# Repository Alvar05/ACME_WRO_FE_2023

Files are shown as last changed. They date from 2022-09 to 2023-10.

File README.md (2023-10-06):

Engineering materials
====
## Introduction

This repository provides information about the building and programming process of our self-driving car for the Future Engineers 2023 competition. Since this is our third year participating in this competition we have updated our robot even more to be more controllable, compact and precise, remaking it almost entirely.

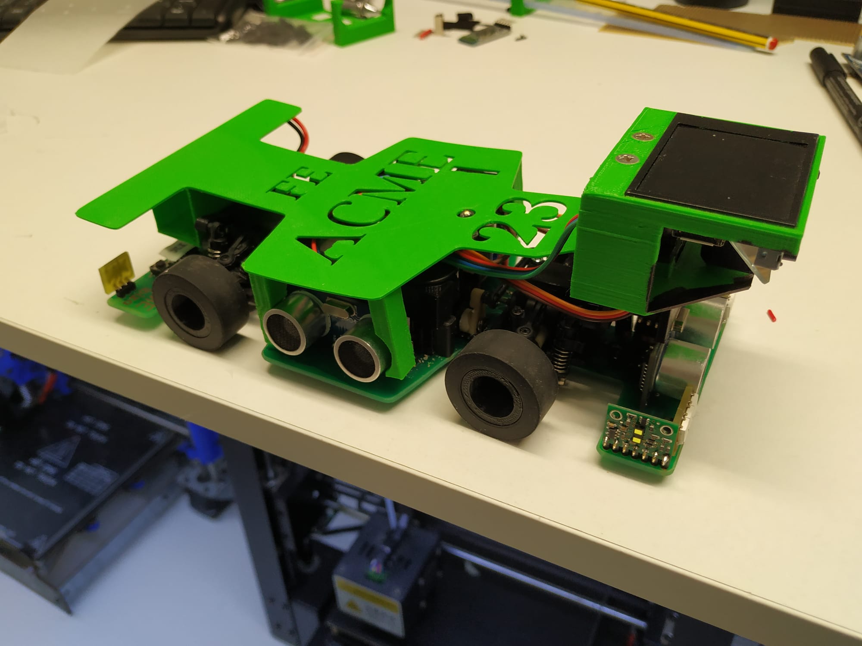
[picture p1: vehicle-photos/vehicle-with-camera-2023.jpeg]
Asembled Vehicle

## Content

* `team-photos` contains 2 photos of the team (an official one and one funny photo).
* `vehicle-photos` contains 6 photos of the vehicle (from every side, top and bottom).
* `video` contains the video.md file with the link to a video with a driving demonstration.
* `schematics` contains schematic diagrams of the electromechanical components, illustrating all the elements (electronic components and motors) used in the vehicle and how they connect to each other.
* `src` contains code of control software for all components which were programmed to participate in the competition.
* `models` contains all the 3D-printed parts of the vehicle. 
* `other` contains the PCBs of the vehicle and the datasheets of all the components.
* `YouTube Channel` All public videos are uploaded at https://www.youtube.com/channel/UCMpIuC9MiNL4U_FDTKrd1CQ

## Structure

This year we are reusing the structure from last year, a RC toy car (the WLtoys k989). We removed the rear differential case to make it front drive, and we put two optical encoders connected to the rear wheels in the new free space.
But the most important change is that we removed the aluminium base and replaced it with our new PCB. This PCB is made by us: we insolated a photo-sensible PCB, put green solder mask on it and soldered all the connections and vias. The components are almost all soldered in SMD (surface mounted) by hand, we even had to use a digital microscope.

## Electronics

The robot consists of three ATMEGA32U4 microcontrollers, so it can be seen as three modules. One microcontroller as the Master, another as the I2C Slave and the last as the Sensors Slave. We chose to use three microcontrollers because we feared that they would be saturated and we could not upload the main code, and in the end we were right, the programs for each use around the 70 - 80% of the maximum program memory.

### Sensors slave

This microcontroller reads the data from three HC-SR04 ultrasonic sensors (in the front, right side and left side) and of three encoders (two on the rear wheels and one directly connected to the motor). It also controls the motor via one IFX9201SG H-bridge motor controller.
The microcontroller connects to the master via SPI communication to send the data from the sensors and receive commands to drive the motor.

### I2C slave
 
This microcontroller connects to all the sensors who use I2C communication: one MPU6050 gyroscope sensor, two VL53L1X TOF sensors (left and right) and the HuskyLens camera. It also controls 10 WS2810B LEDs that act as the vehicle’s headlights, turn signals and brake lights, and a servo that rotates a small mirror that allows the camera to see from left to right.
This microcontroller also sends its sensor data via SPI communication to the master and receives the commands to turn the LEDs on or off.
 
### Master

This microcontroller is in charge of the main program which uses all the information received from the slaves to control the entire robot (mainly the direction servo and the motor) to complete the challenge.

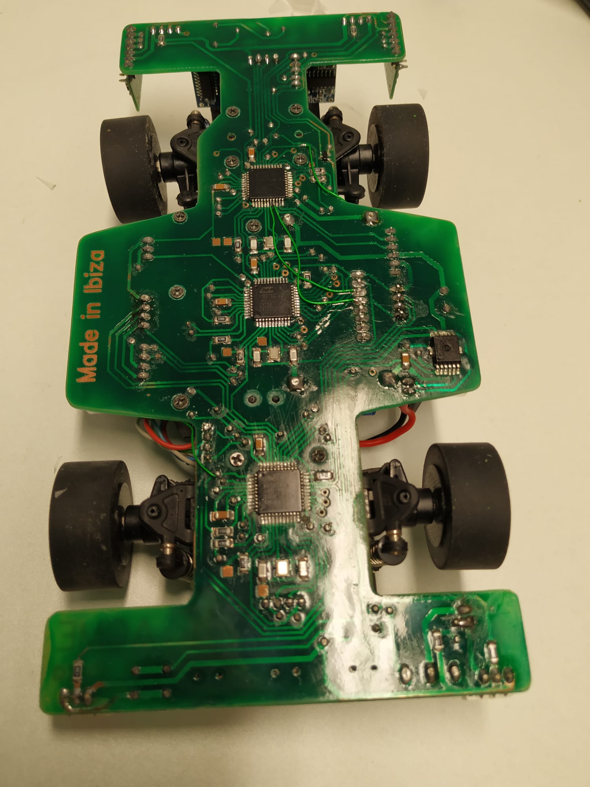
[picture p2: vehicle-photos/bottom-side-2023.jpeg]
PCB Bottom

## Programming modules

Having in mind that there are three programs (for each microcontroller), we can also group parts of all the code in groups regarding its purpose.

### Movement

The movement of the vehicle is done by a series of instructions: The Master 32U4 sends the Sensors 32U4 the command to start the motor at a specific speed, with or without a PID controller that adjusts the speed of the motor based on its encoder so its exactly the one required. The master also changes the speed of the motor doing a exponential acceleration or deceleration when needed. Then reads the data of the MPU6050 from the I2C 32U4 to adjust the direction servo with another PID controller to drive straight. Or it moves the servo to turn the car if needed.

### Detecting walls

We mainly use the ultrasonic and TOF sensors to detect distance to walls, to know if we passed a corner and to know the turn direction.
When we pass a corner one of the lateral sensors detects a higher distance, that means there is no wall in that side, that way we know we have to turn to that side.
They can also be used to detect a signal without knowing the color.
The problems with these sensors are that the ultrasonic are very slow for our possible speeds and because the walls are black, little light is reflected to the TOF sensors (the walls we used in Ibiza reflected almost nothing) and the readings may be erratic or imprecise, but we do not know of other types of distance sensors to read walls.

### Detecting the color signals

We use a HuskyLens AI camera with the capability to recognize faces and objects, but most importantly for us, it can recognize colors. Its mounted on a 3D-printed case with an integrated servo that turns a little mirror that reflects the image received by the camera, this way it can view from left to right, around 180º. This allows us to mount the camera facing downwards and make it more compact. The only problem is that this method transposes the image and it needs to be corrected in code.
When the robot detects that it passed a corner, it turns the mirror to view what is in the next sector and the camera reads the color and position of the signals. We simplified the number of possible positions of the signals to 11, ignoring if they are in the left or right lane (only taking into account if they are in the rear, middle or front), because our vehicle is small enough that it can pass between any position of the signals.
The I2C 32U4, the one with the camera, then sends the number we assigned of the specific position in which the signals are to the Master, which saves this position for the other two laps (this way we can go faster because we do not need to read the positions again) and turns the car to position itself on the correct side.

## Debugging with graphs and telemetry

For debugging purposes we included a HC-05 bluetooth module in the vehicle, only used during testing and debuggin, during the competition it will be disconnected. For ease of analyzing the information sent by the robot we use a graphing application made with Python by our friend Maria Pilligua uploaded to her [GitHub repository](https://github.com/mpilligua/app_wro). With this we can see values like the speed or the distance counted from the encoders and view it in the style of Formula 1 telemetry which is more practical for comparing it to earlier tests.

## Code building, compiling and uploading process

We programmed all using the Arduino IDE like any Arduino board, but because we use the 32U4 microcontrollers directly we have to flash the bootloader to each 32U4. We flashed the Arduino Leonardo bootloader because it uses this microcontroller and we are very familiar with it. The process for flashing it requires you to connect the 32U4 to another Arduino using the ICSP communication, then the normal Arduino acts as an ISP programmer (using the example code ArduinoISP) and flashes your 32U4 with the selected bootloader.
Because this was our first time doing this we used this [SparkFun guide](https://learn.sparkfun.com/tutorials/installing-an-arduino-bootloader/all) and this [Arduino guide](https://docs.arduino.cc/built-in-examples/arduino-isp/ArduinoISP).

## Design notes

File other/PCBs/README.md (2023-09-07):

This directory contains all the gerber files for the PCBs used in the car:

* `Frontal LEDs PCB`
* `Rear LEDs PCB`
* `Main PCB` - It has vias to connect extra pins to the microcontrollers if needed, but have to be soldered with external cables. It also has 3 cables as bridges (SS_A and bumper pins (not used)).
* `Encoders PCB` - Do not make the big holes for the encoders, those are an error of the program and are not supposed to be there.

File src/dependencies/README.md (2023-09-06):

These are the required libraries (third-party) to compile the code to the controllers. All credits are to the respective creators of each library.

* `HUSKYLENS:` Library for controlling the HuskyLens Camera
* `MPU6050_light:` Lightweight library for controlling the MPU6050 Gyroscope-accelerometer
* `NewPing:` Library for controlling HC-04 ultrasonic sensors
* `VL53L1X:` Library for controlling Time Of Flight (IR laser) sensors
* `light_WS2812:` Lightweight library for controlling WS2812B LEDs

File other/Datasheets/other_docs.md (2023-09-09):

* `HuskyLens:` https://wiki.dfrobot.com/HUSKYLENS_V1.0_SKU_SEN0305_SEN0336
* `DC Motor:` The motor came with the MiniZ RC car and we don't have its datasheet
* `Hall effect motor encoder:` https://www.pololu.com/product/3081

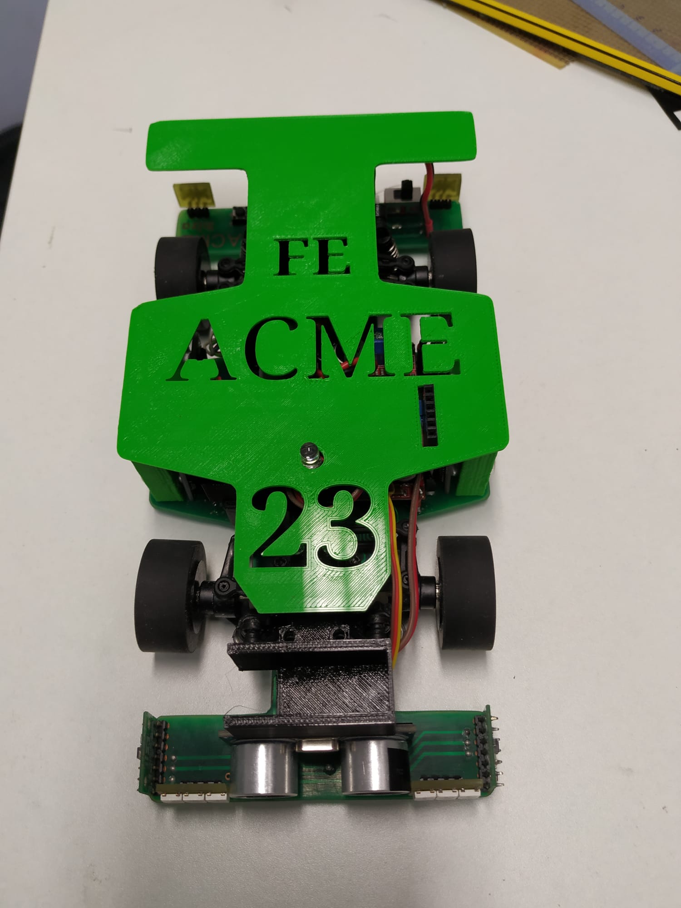
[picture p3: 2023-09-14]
vehicle-photos/top-side-2023.jpeg

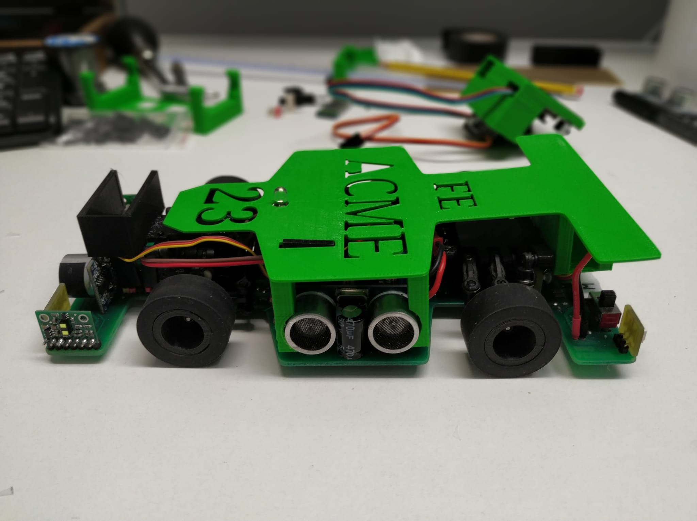
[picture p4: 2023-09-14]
vehicle-photos/left-side-2023.jpeg

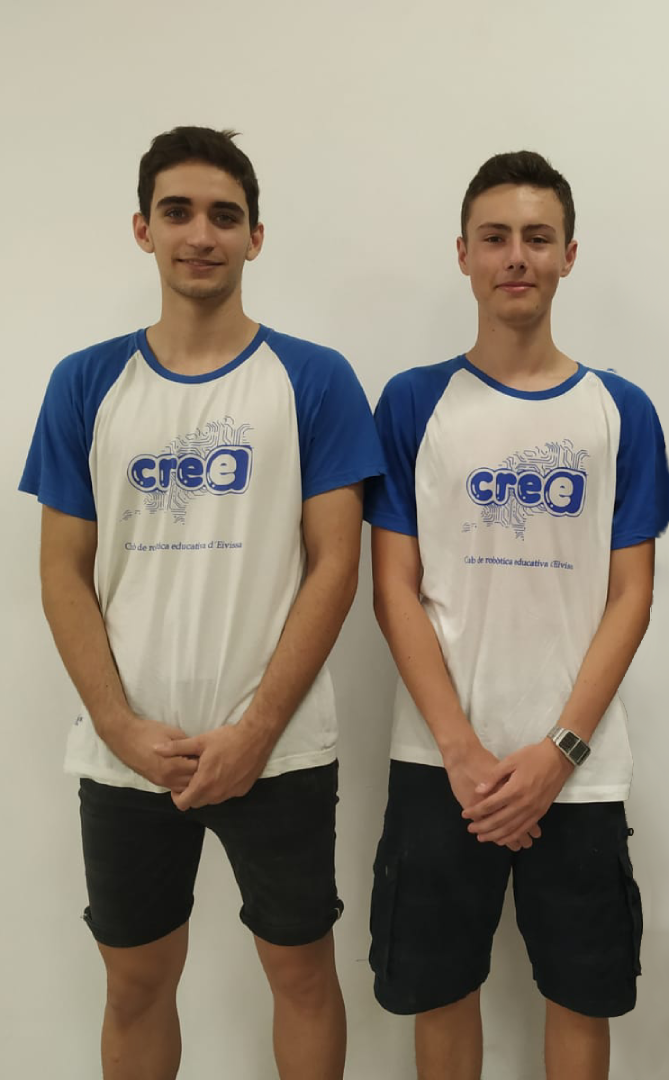
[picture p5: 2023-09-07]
team-photos/official-photo.png

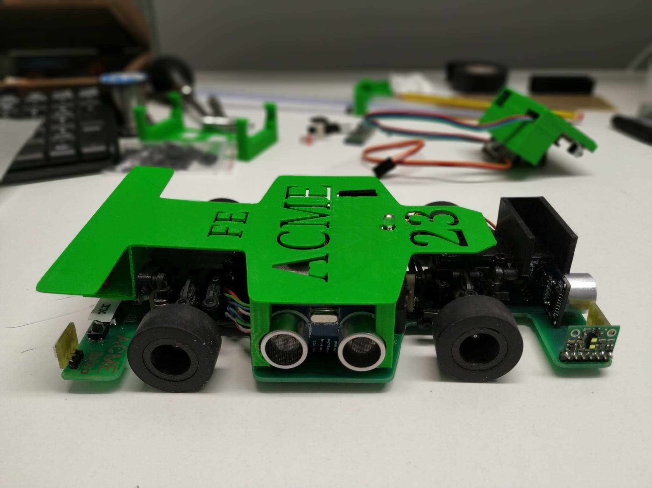
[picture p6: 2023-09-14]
vehicle-photos/right-side-2023.jpeg

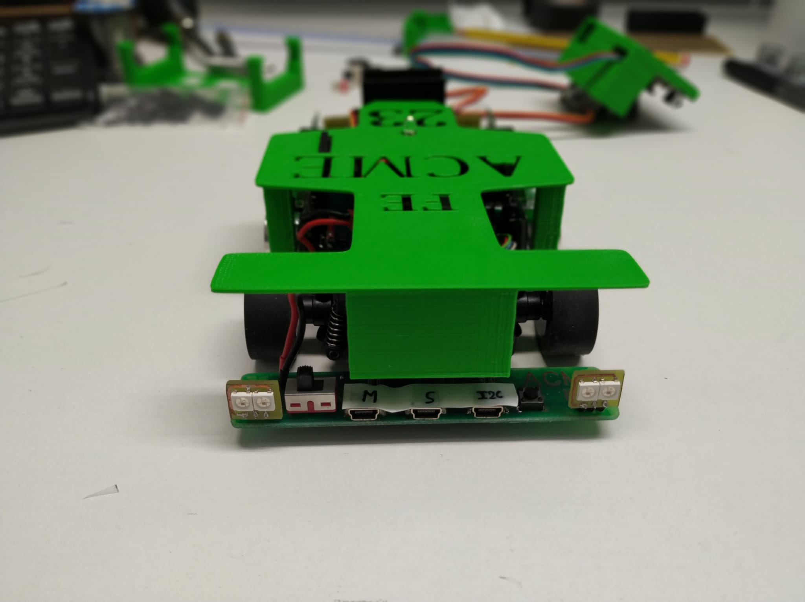
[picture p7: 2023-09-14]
vehicle-photos/rear-2023.jpeg

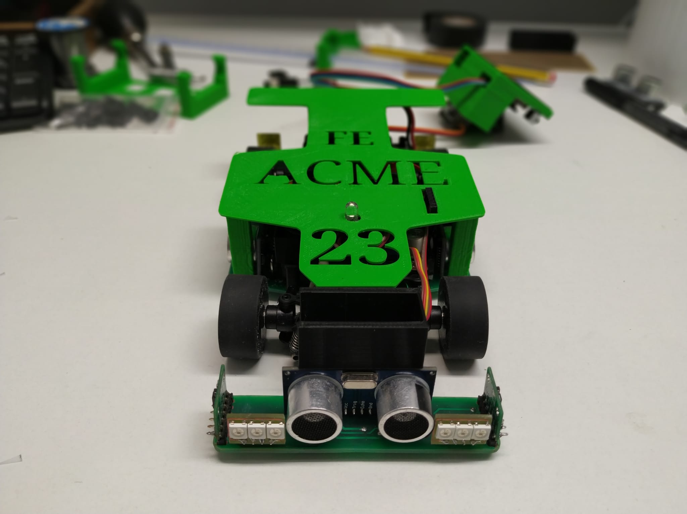
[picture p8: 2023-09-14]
vehicle-photos/front-2023.jpeg

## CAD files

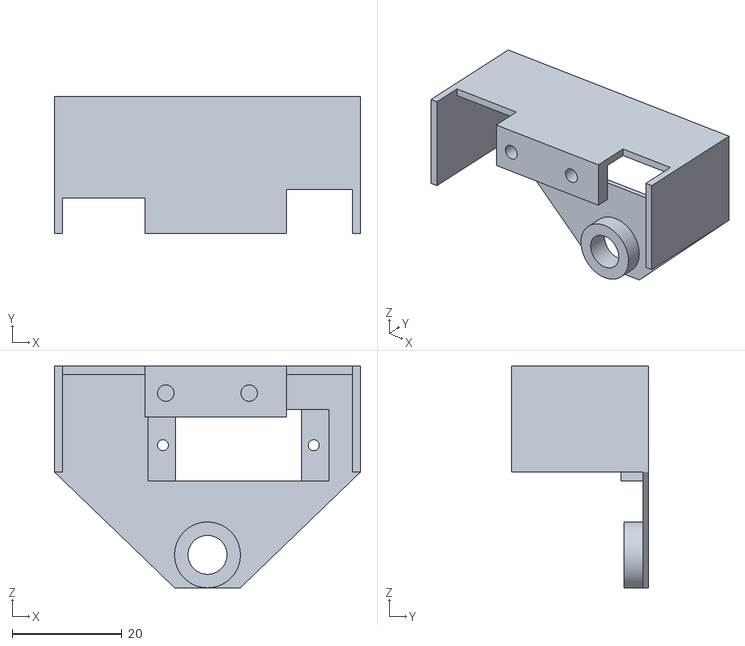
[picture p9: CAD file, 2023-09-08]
models/camera-and-mirror/camera-mirror-support.stl
55.8 x 25.0 x 40.4

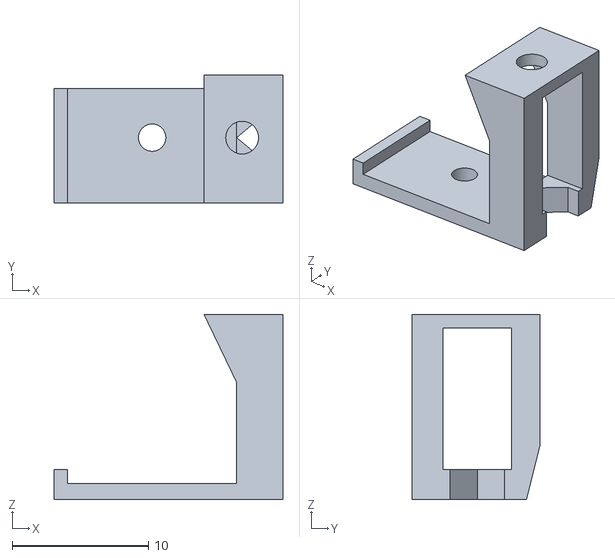
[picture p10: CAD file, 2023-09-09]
models/encoders/motor-encoder-bracket.stl
16.8 x 9.40 x 13.6

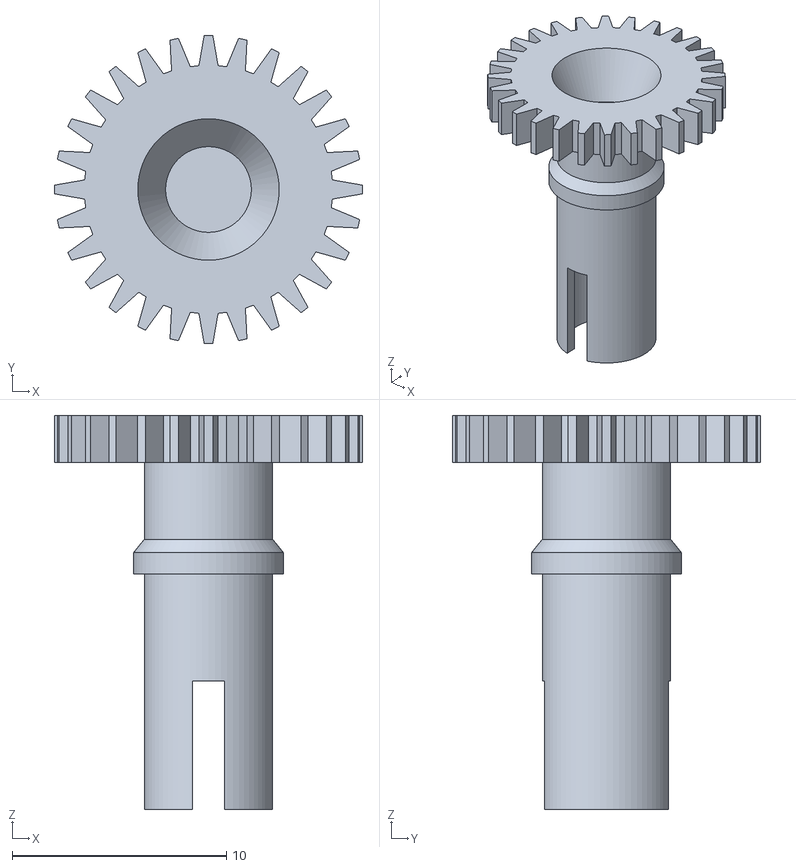
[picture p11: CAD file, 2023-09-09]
models/encoders/tyre-encoders/gear-to-cardan.stl
14.4 x 14.4 x 18.4

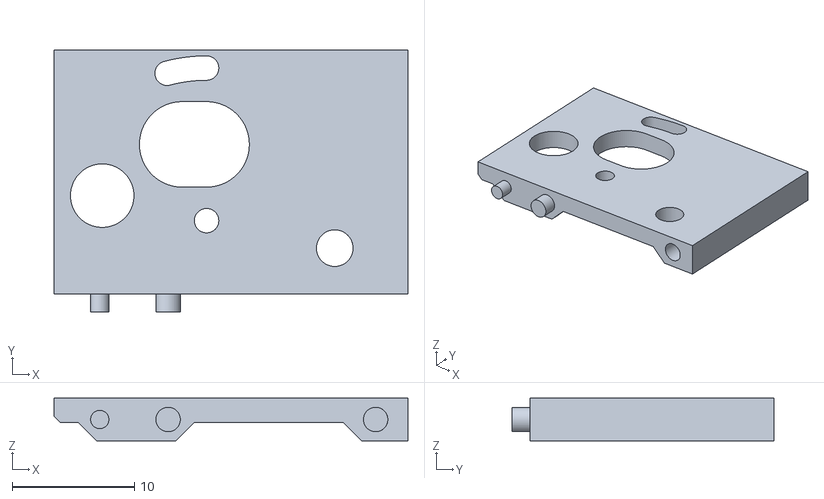
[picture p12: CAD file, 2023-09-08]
models/motor-bracket/motor-bracket-part1.stl
29.0 x 21.5 x 3.50

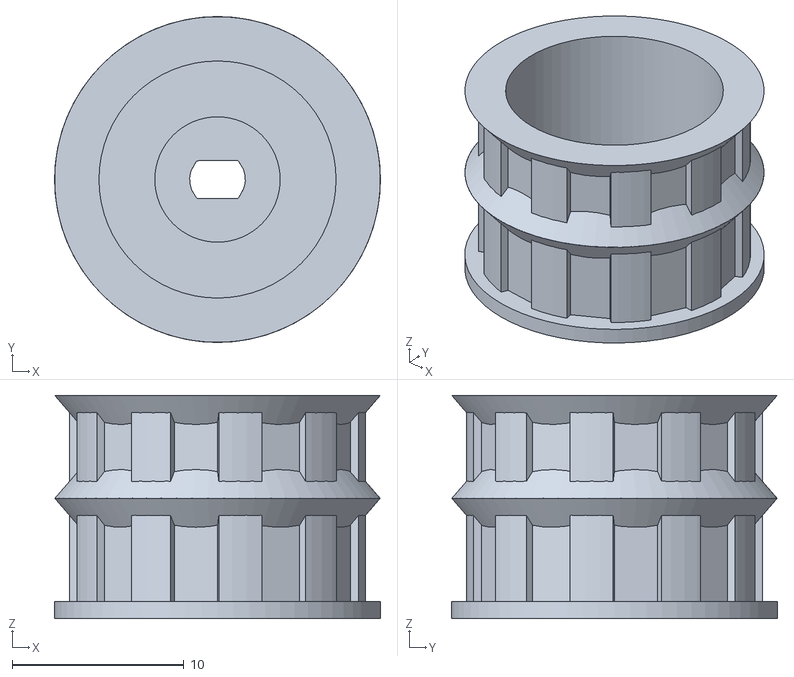
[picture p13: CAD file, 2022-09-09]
models/Wheels.stl
19.0 x 19.0 x 13.0

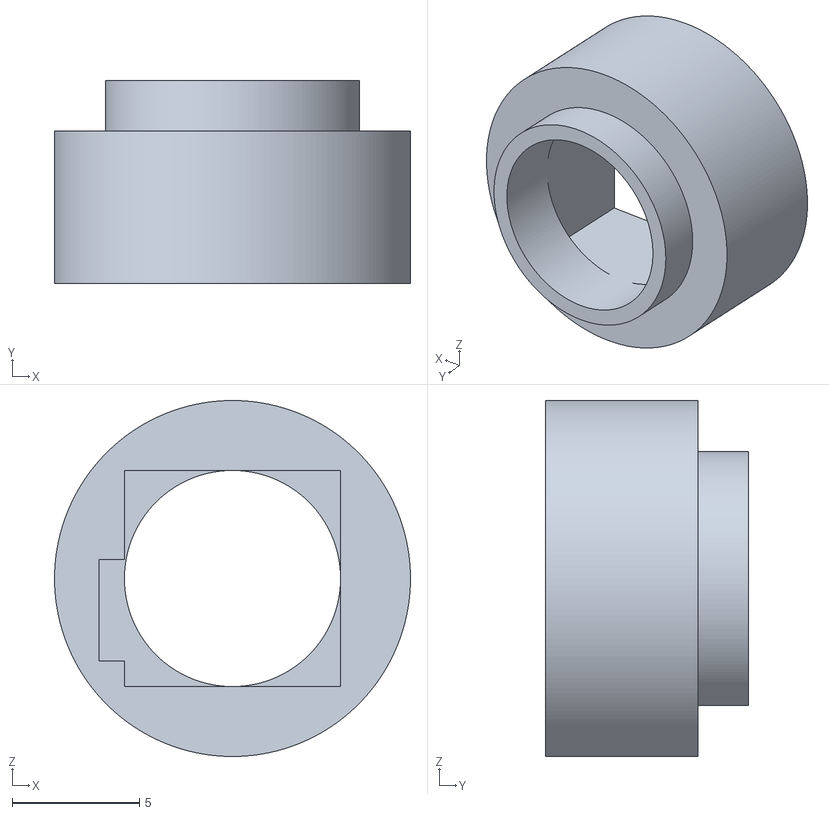
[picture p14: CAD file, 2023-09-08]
models/camera-and-mirror/camera-support.stl
14.0 x 8.00 x 14.0

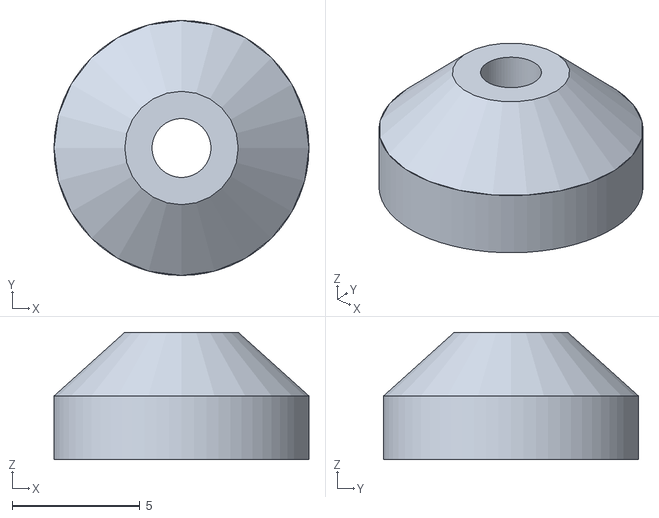
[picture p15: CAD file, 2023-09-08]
models/encoders/magnet-holder-motor-encoder.stl
10.00 x 10.0 x 5.00

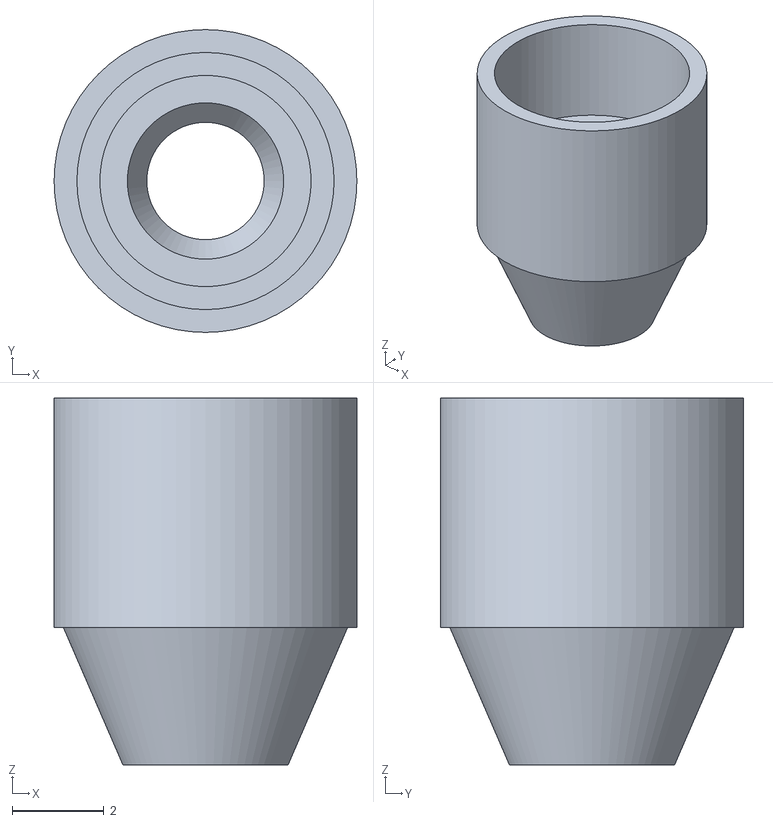
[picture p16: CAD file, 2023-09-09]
models/encoders/tyre-encoders/separator-piece-2.stl
6.60 x 6.60 x 8.00

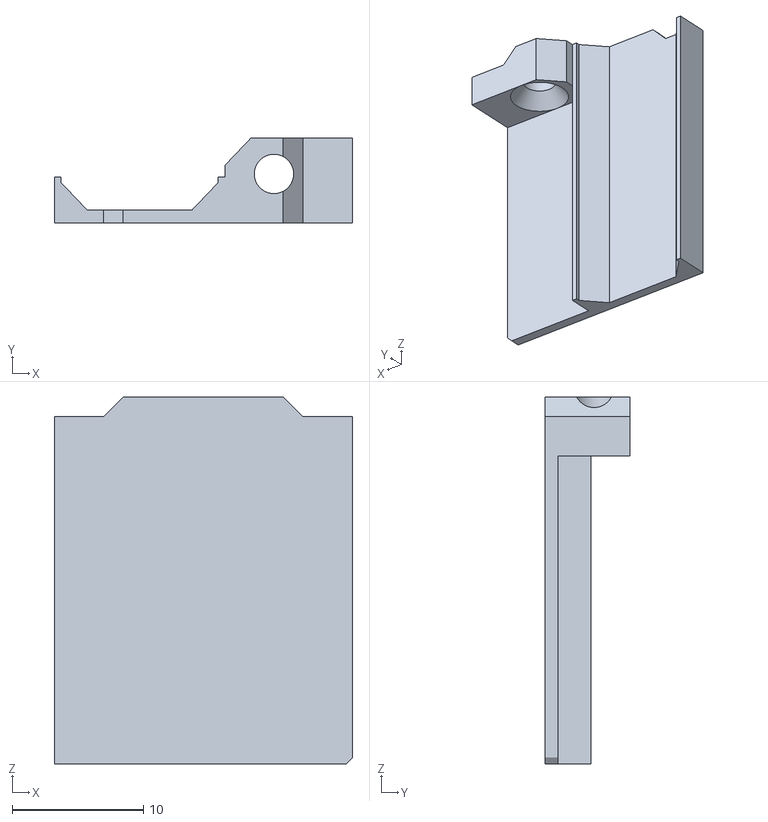
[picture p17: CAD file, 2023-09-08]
models/motor-bracket/motor-bracket-part2.stl
22.8 x 6.50 x 28.0

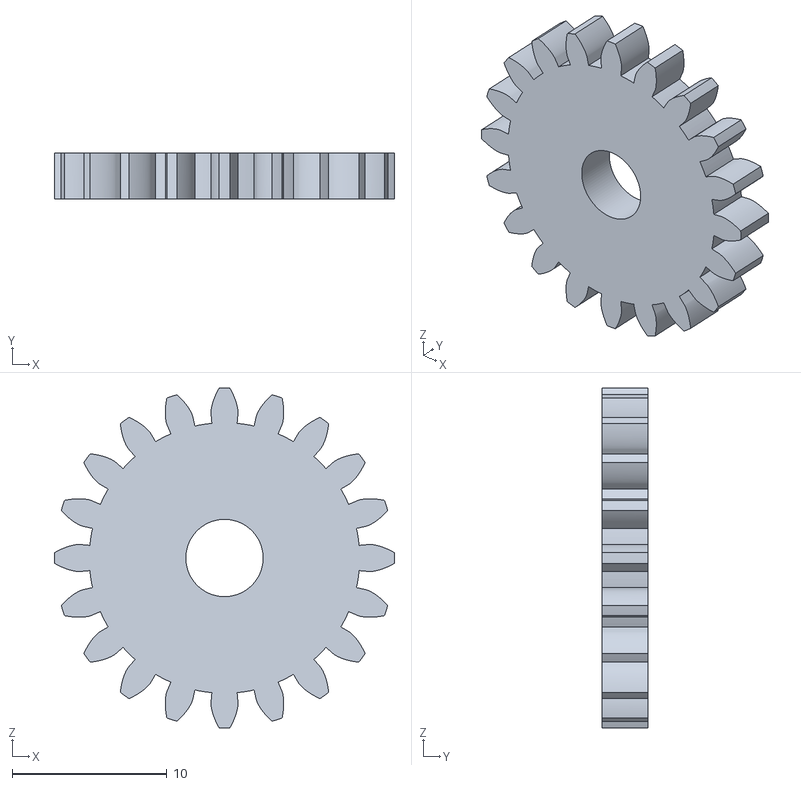
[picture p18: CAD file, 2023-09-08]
models/camera-and-mirror/servo-gear.stl
22.0 x 3.00 x 22.0

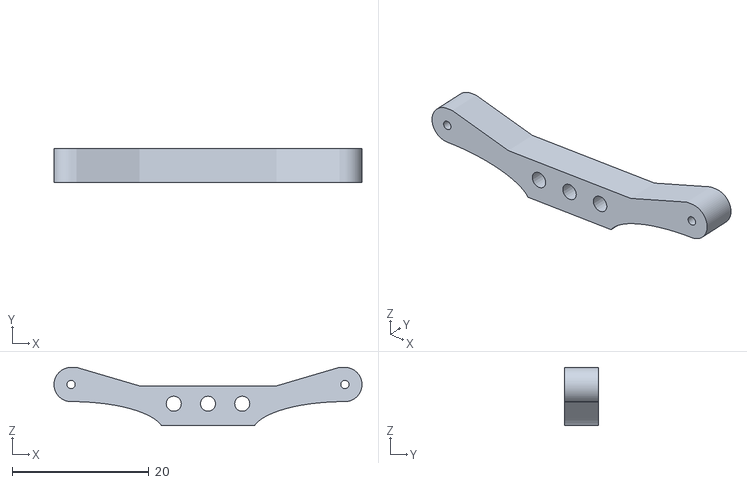
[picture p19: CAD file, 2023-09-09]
models/encoders/tyre-encoders/shock-absorber-support.stl
45.0 x 5.00 x 8.50

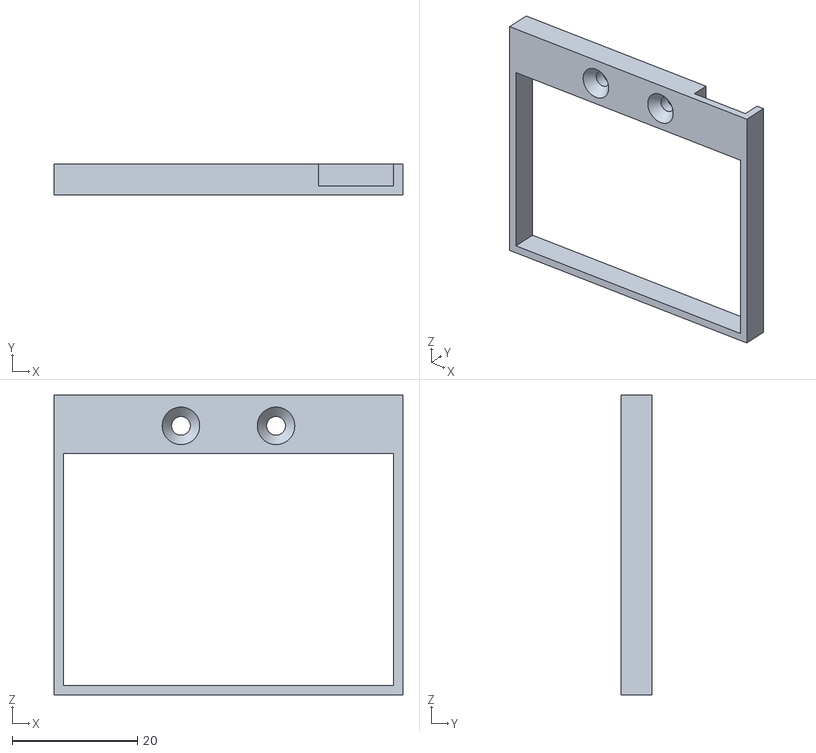
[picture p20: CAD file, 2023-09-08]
models/camera-and-mirror/camera-case.stl
55.8 x 5.00 x 47.9

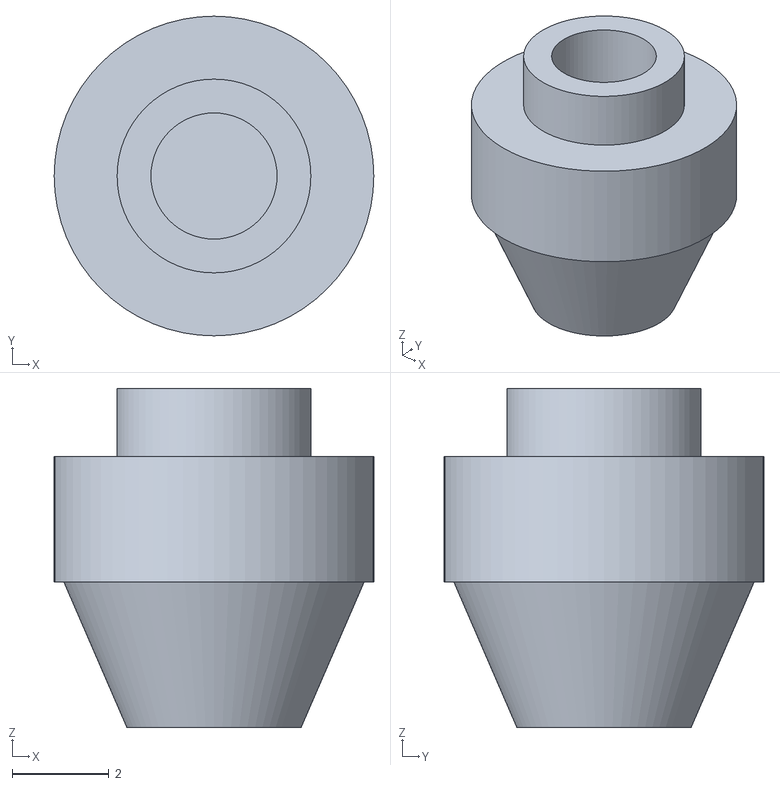
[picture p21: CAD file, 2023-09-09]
models/encoders/tyre-encoders/separator-piece-1.stl
6.60 x 6.60 x 7.00

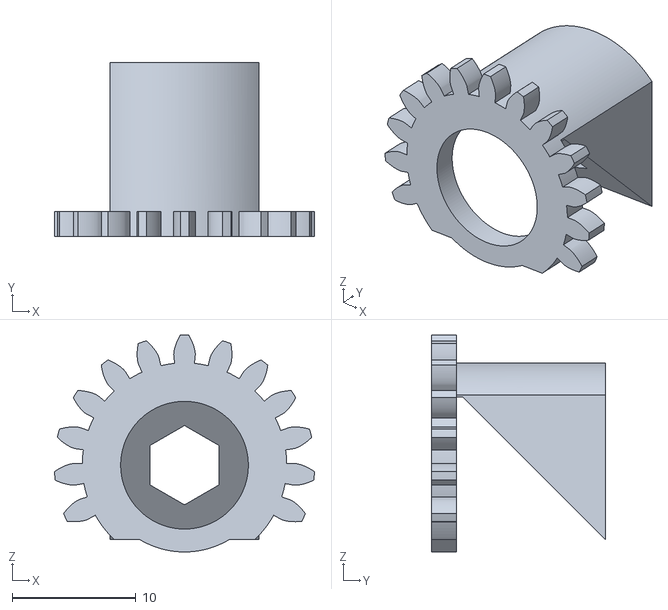
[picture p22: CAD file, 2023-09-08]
models/camera-and-mirror/mirror-support.stl
21.0 x 14.0 x 17.5

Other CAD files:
models/encoders/tyre-encoders/encoder-cage-bottom.stl
models/encoders/tyre-encoders/encoder-cage-top.stl

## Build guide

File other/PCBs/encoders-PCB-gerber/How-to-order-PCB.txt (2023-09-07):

How to Order PCB

Please refer to:
https://docs.easyeda.com/en/PCB/Order-PCB

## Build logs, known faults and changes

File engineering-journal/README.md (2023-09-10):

This folder contains the engineering journal both in english and spanish.
* `engineering-journal-ACME-en` The engineering journal in english, it explains the process used to achieve our final vehicle.
* `cuaderno-ingenieria-ACME-es` The same engineering journal in spanish. / El mismo cuaderno de ingenieria en español, explica el proceso usado para llegar a nuestro vehiculo final.
* `other-photos` Includes other photos from the process of creation of the vehicle.

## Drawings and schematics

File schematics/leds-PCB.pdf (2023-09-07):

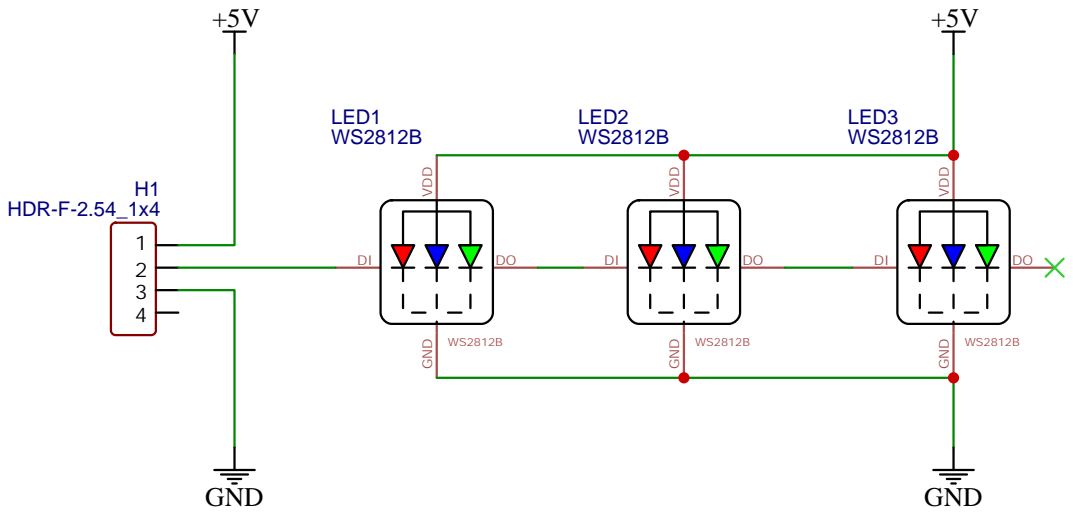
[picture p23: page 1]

Drawn By: Marc Costa

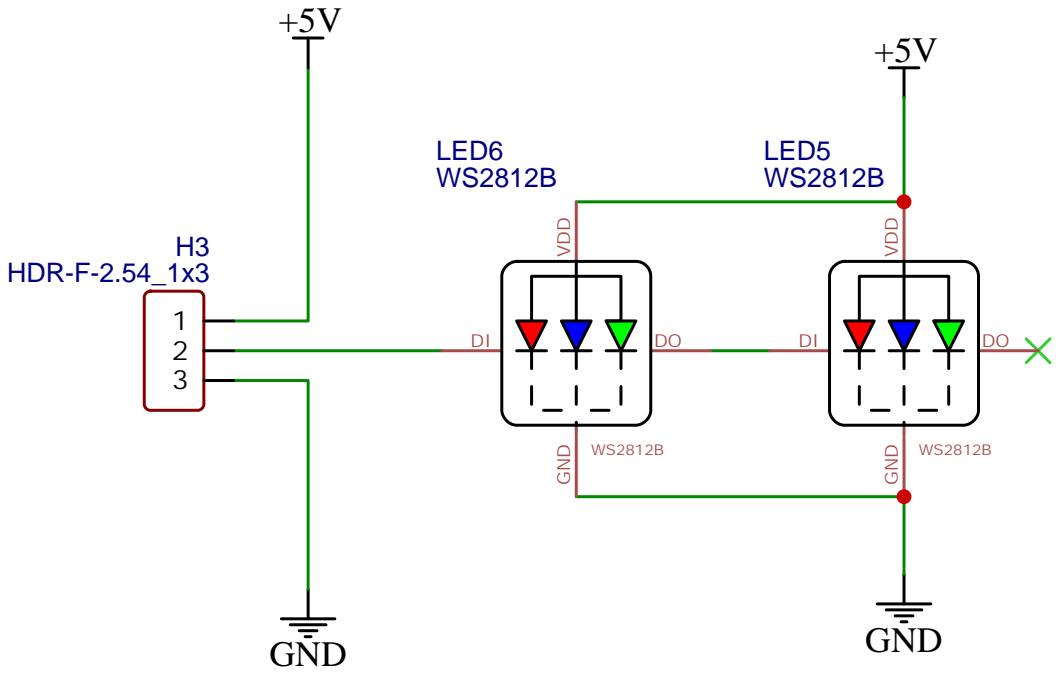
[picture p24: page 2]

Drawn By: Marc Costa

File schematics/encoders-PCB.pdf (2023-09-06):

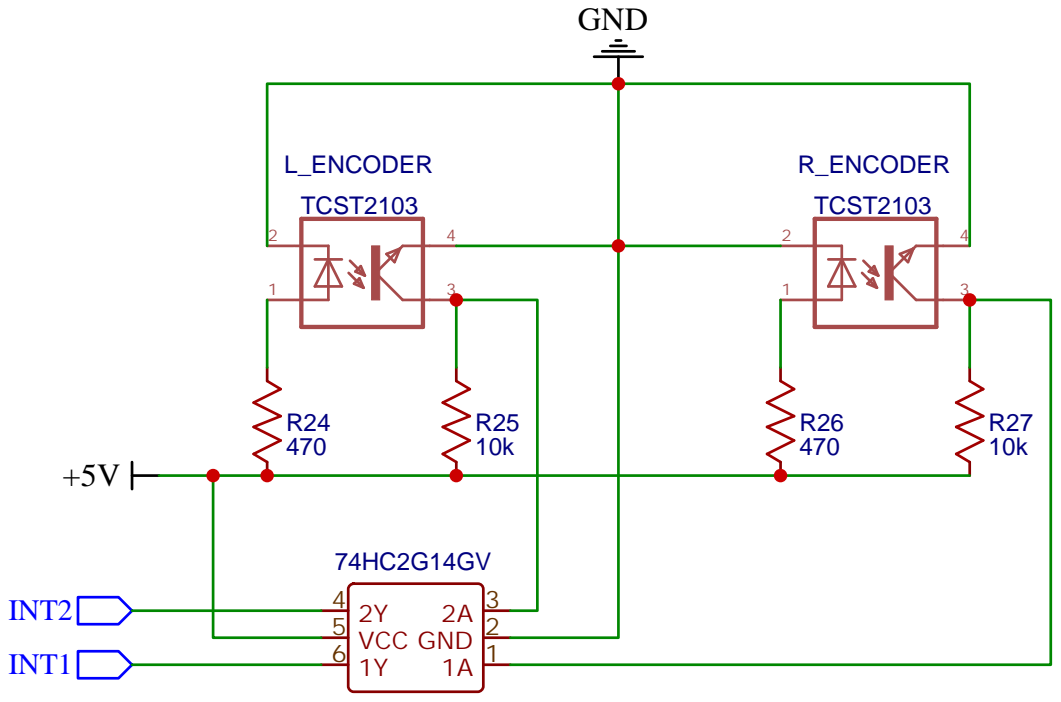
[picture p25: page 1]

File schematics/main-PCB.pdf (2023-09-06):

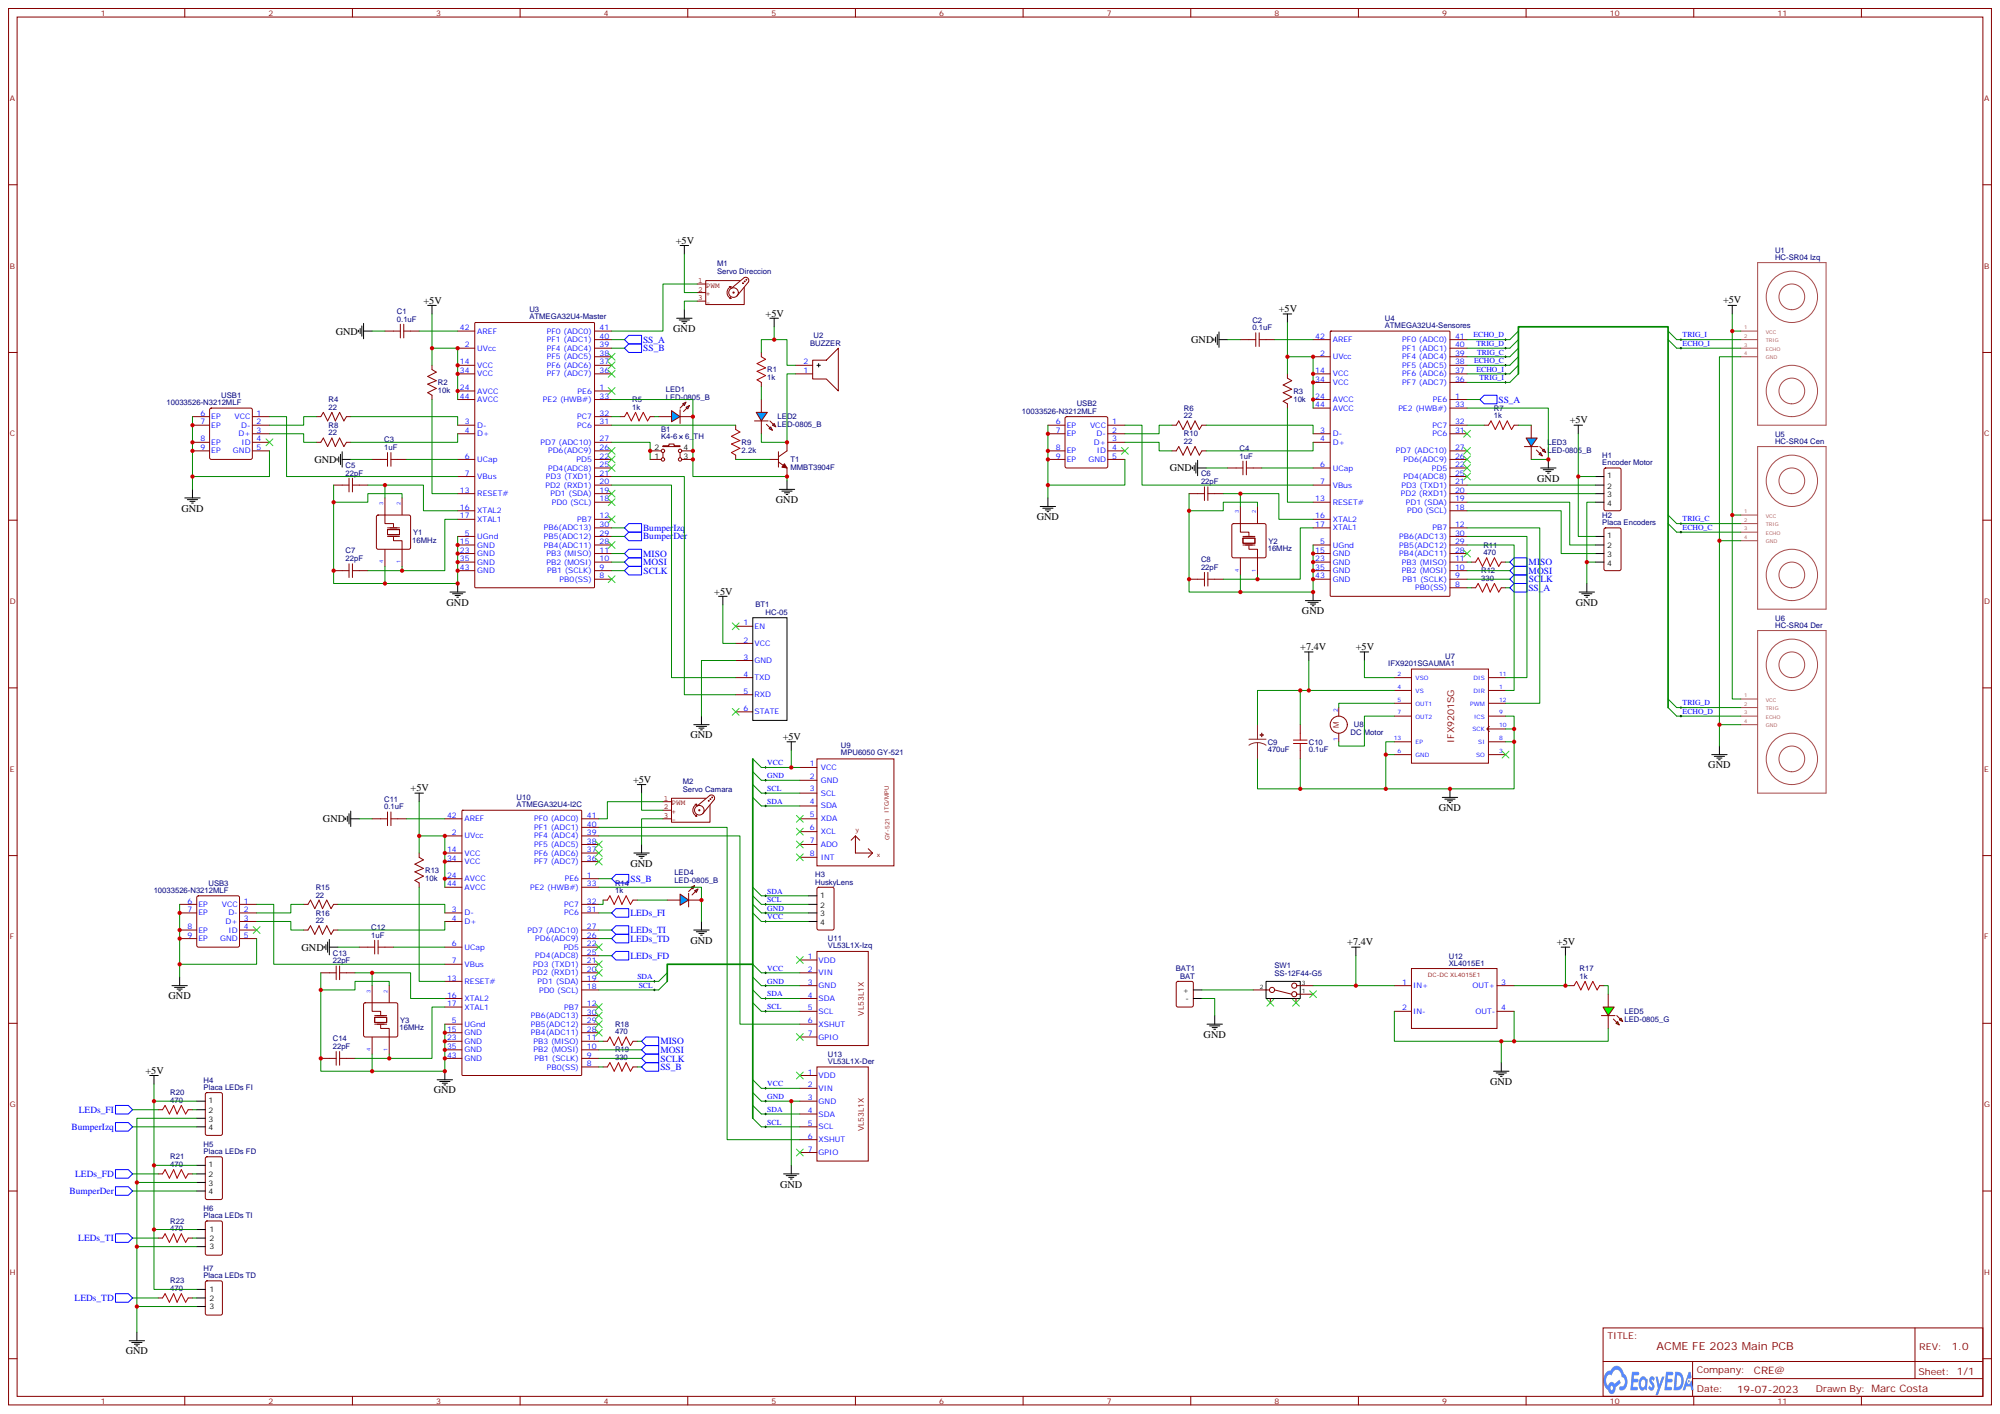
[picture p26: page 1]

Drawn By: Marc Costa

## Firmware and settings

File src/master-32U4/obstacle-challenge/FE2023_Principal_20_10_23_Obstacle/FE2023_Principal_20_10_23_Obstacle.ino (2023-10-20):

#include "definiciones.h"


bool robotActivo = false;
int errores = 0;
byte speed = 20;
unsigned long buenaTramaA = 0;
unsigned long errorTramaA = 0;
unsigned long buenaTramaB = 0;
unsigned long errorTramaB = 0;
bool estadoFreno = 1;
long distanciaBT;
long tiempoLED;
int angPID = 0;
bool activePID = true;

Servo direccion;
MPU6050 mpu(Wire);

void setup(void) {
  direccion.attach(DIR);
  pinMode(BTN, INPUT_PULLUP);
  pinMode(LED, OUTPUT);
  setupSPI();
  digitalWrite(LED, 1);
  digitalWrite(BUZZ, 1);
  direccion.write(90 + offsetMPU);
  delay(100);
  digitalWrite(BUZZ, 0);
  setupMPU();
  tiempoLED = millis() + 500;
  while ((i2c.TOF[0] == 0) or (i2c.TOF[1] == 0)) {
    updateMPU();
    updateSPI();
    updateLed();
  }
  digitalWrite(BUZZ, 1);
  delay(50);
  digitalWrite(BUZZ, 0);
  delay(50);
  digitalWrite(BUZZ, 1);
  delay(50);
  digitalWrite(BUZZ, 0);
  updateMPU();
  resetCarAngle();
  setDireccionCamara(90);
  activarHL();
  activarUS("F");
  while (digitalRead(BTN)) {
    updateRobot();
    if (verdeCerca()) intermitente('I');
    else if (rojoCerca()) intermitente('D');
    else intermitente('A');
  }
  intermitente('A');
  delay(1000);
  updateMPU();
  resetCarAngle();
  moveInicio();
  bool vueltaLectura = true; 
  for (uint8_t i = 0; i < 2; i++) {
    if (sentidoRonda == 1) moveSector(90, sectorRonda[1], sentidoRonda, 1, vueltaLectura);
    else moveSector(270, sectorRonda[1], sentidoRonda, 1, vueltaLectura);
    moveSector(180, sectorRonda[2], sentidoRonda, 2, vueltaLectura);
    if (sentidoRonda == 1) moveSector(270, sectorRonda[3], sentidoRonda, 3, vueltaLectura);
    else moveSector(90, sectorRonda[3], sentidoRonda, 3, vueltaLectura);
    if (i == 0) {
      moveSector(0, sectorRonda[0], sentidoRonda, 0, false);
      vueltaLectura = false;
      vuelta++;
    }
  }
  byte ultimoBloque = bloqueCerca(sectorRonda[0]);
  if (ultimoBloque == 0) {
    ultimoBloque = mirarUltimoBloque(sectorRonda[3]);
    if (ultimoBloque == 1) {  // Ultimo Bloque Verde
      moveSector(0, sectorRonda[0], sentidoRonda, 0, false);
      vuelta++;
      if (sentidoRonda == 1) moveSector(90, sectorRonda[1], sentidoRonda, 1, false);
      else moveSector(270, sectorRonda[1], sentidoRonda, 1, false);
      moveSector(180, sectorRonda[2], sentidoRonda, 2, false);
      if (sentidoRonda == 1) moveSector(270, sectorRonda[3], sentidoRonda, 3, false);
      else moveSector(90, sectorRonda[3], sentidoRonda, 3, false);
      moveSector(0, sectorRonda[0], sentidoRonda, 0, false);
      robotStop();
    }
    else {
      for (uint8_t i = 0; i < sizeof(sectorRonda); i++) {
        if (sectorRonda[i] == 1) sectorRonda[i] = 5;
        else if (sectorRonda[i] == 2) sectorRonda[i] = 6;
        else if (sectorRonda[i] == 5) sectorRonda[i] = 1;
        else if (sectorRonda[i] == 6) sectorRonda[i] = 2;
        else if (sectorRonda[i] == 8) sectorRonda[i] = 10;
        else if (sectorRonda[i] == 10) sectorRonda[i] = 8;
      }
      giroEnlace(distAnterior, 550, 0, sentidoRonda);
      moveDistancia(500, vMinSector, vMinSector);
      while (!commandFinished) updateRobot();
      if (sentidoRonda == 1) {
        intermitente('D');
        setVelocidad(10);
        activePID = false;
        motorResetCount("DI");
        while (abs(abs(getCarAngle()) - 180) > 10) {
          pidCurva(250, 2, 0, 0);
          updateRobot();
        }
        angPID = 180;
        activePID = true;
        dirAnteriorCurva = 180;
        moveDistancia(100, vMinSector, vMinSector);
        while (!commandFinished) updateRobot();
        while (i2c.TOF[0] < mediaTOFpared) updateRobot();
        distAnterior = 200;
        vuelta++;
        sentidoRonda = -1;
        moveSector(90, sectorRonda[3], sentidoRonda, 3, false);
        moveSector(0, sectorRonda[2], sentidoRonda, 2, false);
        moveSector(270, sectorRonda[1], sentidoRonda, 1, false);
        moveSector(180, sectorRonda[0], sentidoRonda, 0, false);
      }
      else {
        intermitente('I');
        setVelocidad(10);
        activePID = false;
        motorResetCount("DI");
        while (abs(abs(getCarAngle()) - 180) > 10) {
          pidCurva(-250, 2, 0, 0);
          updateRobot();
        }
        angPID = 180;
        activePID = true;
        dirAnteriorCurva = 180;
        moveDistancia(100, vMinSector, vMinSector);
        while (!commandFinished) updateRobot();
        while (i2c.TOF[1] < mediaTOFpared) updateRobot();
        distAnterior = 200;
        vuelta++;
        sentidoRonda = 1;
        moveSector(270, sectorRonda[3], sentidoRonda, 3, false);
        moveSector(0, sectorRonda[2], sentidoRonda, 2, false);
        moveSector(90, sectorRonda[1], sentidoRonda, 1, false);
        moveSector(180, sectorRonda[0], sentidoRonda, 0, false);
      }
    }
  }
  else if (ultimoBloque == 2) {  // Last obstacle red
    int sectorCambio = sectorRonda[0];
    for (uint8_t i = 0; i < sizeof(sectorRonda); i++) {
      if (sectorRonda[i] == 1) sectorRonda[i] = 5;
      else if (sectorRonda[i] == 2) sectorRonda[i] = 6;
      else if (sectorRonda[i] == 5) sectorRonda[i] = 1;
      else if (sectorRonda[i] == 6) sectorRonda[i] = 2;
      else if (sectorRonda[i] == 8) sectorRonda[i] = 10;
      else if (sectorRonda[i] == 10) sectorRonda[i] = 8;
    }
    if (sentidoRonda == 1) {
      giroEnlace(distAnterior, 0, 0, sentidoRonda);
      intermitente('I');
      moveDistancia(200, vMinSector, vMinSector);
      while (!commandFinished) updateRobot();
      if (sectorCambio == 4) {
        while (i2c.TOF[0] > mediaTOFbloque) updateRobot();
        moveDistancia(200, vMinSector, vMinSector);
        while (!commandFinished) updateRobot();
        setVelocidad(10);
        activePID = false;
        motorResetCount("DI");
        while (abs(abs(getCarAngle()) - 90) > 10) {
          pidCurva(-150, 2, 0, 0);
          updateRobot();
        }
        angPID = 270;
        activePID = true;
        dirAnteriorCurva = -90;
        moveDistancia(100, vMinSector, vMinSector);
        while (!commandFinished) updateRobot();
        setVelocidad(10);
        activePID = false;
        motorResetCount("DI");
        while (abs(abs(getCarAngle()) - 180) > 10) {
          pidCurva(-150, 2, 0, 0);
          updateRobot();
        }
        angPID = 180;
        activePID = true;
        dirAnteriorCurva = 180;
        moveDistancia(450, vMinSector, vMinSector);
        while (!commandFinished) updateRobot();
      }
      else {
        setVelocidad(10);
        activePID = false;
        motorResetCount("DI");
        while (abs(abs(getCarAngle()) - 180) > 10) {
          pidCurva(-250, 2, 0, 0);
          updateRobot();
        }
        angPID = 180;
        activePID = true;
        dirAnteriorCurva = 180;
        moveDistancia(100, vMinSector, vMinSector);
        while (!commandFinished) updateRobot();
        while (i2c.TOF[0] > mediaTOFbloque) updateRobot();
      }
      distAnterior = 800;
      vuelta++;
      sentidoRonda = -1;
      moveSector(90, sectorRonda[3], sentidoRonda, 3, false);
      moveSector(0, sectorRonda[2], sentidoRonda, 2, false);
      moveSector(270, sectorRonda[1], sentidoRonda, 1, false);
      moveSector(180, sectorRonda[0], sentidoRonda, 0, false);
    }
    else {
      giroEnlace(distAnterior, 550, 0, sentidoRonda);
      intermitente('I');
      moveDistancia(200, vMinSector, vMinSector);
      while (!commandFinished) updateRobot();
      if (sectorCambio == 4) {
        while (i2c.TOF[0] > mediaTOFbloque) updateRobot();
        moveDistancia(200, vMinSector, vMinSector);
        while (!commandFinished) updateRobot();
        setVelocidad(10);
        activePID = false;
        motorResetCount("DI");
        while (abs(abs(getCarAngle()) - 90) > 10) {
          pidCurva(-150, 2, 0, 0);
          updateRobot();
        }
        angPID = 270;
        activePID = true;
        dirAnteriorCurva = -90;
        moveDistancia(100, vMinSector, vMinSector);
        while (!commandFinished) updateRobot();
        setVelocidad(10);
        activePID = false;
        motorResetCount("DI");
        while (abs(abs(getCarAngle()) - 180) > 10) {
          pidCurva(-150, 2, 0, 0);
          updateRobot();
        }
        angPID = 180;
        activePID = true;
        dirAnteriorCurva = 180;
        moveDistancia(450, vMinSector, vMinSector);
        while (!commandFinished) updateRobot();
      }
      else{
        setVelocidad(10);
        activePID = false;
        motorResetCount("DI");
        while (abs(abs(getCarAngle()) - 180) > 10) {
          pidCurva(-250, 2, 0, 0);
          updateRobot();
        }
        angPID = 180;
        activePID = true;
        dirAnteriorCurva = 180;
        moveDistancia(100, vMinSector, vMinSector);
        while (!commandFinished) updateRobot();
        while (i2c.TOF[1] < mediaTOFpared) updateRobot();
      }
      distAnterior = 200;
      vuelta++;
      sentidoRonda = 1;
      moveSector(270, sectorRonda[3], sentidoRonda, 3, false);
      moveSector(0, sectorRonda[2], sentidoRonda, 2, false);
      moveSector(90, sectorRonda[1], sentidoRonda, 1, false);
      moveSector(180, sectorRonda[0], sentidoRonda, 0, false);
    }
  }
  else {  // Last obstacle green
    moveSector(0, sectorRonda[0], sentidoRonda, 0, false);
    vuelta++;
    if (sentidoRonda == 1) moveSector(90, sectorRonda[1], sentidoRonda, 1, false);
    else moveSector(270, sectorRonda[1], sentidoRonda, 1, false);
    moveSector(180, sectorRonda[2], sentidoRonda, 2, false);
    if (sentidoRonda == 1) moveSector(270, sectorRonda[3], sentidoRonda, 3, false);
    else moveSector(90, sectorRonda[3], sentidoRonda, 3, false);
    moveSector(0, sectorRonda[0], sentidoRonda, 0, false);
    robotStop();
  }
  robotStop();
}

void loop(void) {
  updateRobot();
}

void updateRobot() {
  updateMPU();
  if (activePID) pidGyro(angPID, 2, 0, 0);
  enviarSPIA();
  enviarSPIB();
  updateLed();
  updateBeep();
}

void moveInicio() {
  motorStart(7);
  desactivarHL();
  if (verdeCerca()) {
    intermitente('I');
    while (abs(getCarAngle()) < 70) {
      updateMPU();
      enviarSPIA();
      enviarSPIB();
      updateLed();
      updateBeep();
      pidGyro(265, 2, 0, 0);
    }
    intermitente('D');
    while (abs(getCarAngle()) > 5 or i2c.TOF[1] > mediaTOFbloque) {
      updateMPU();
      enviarSPIA();
      enviarSPIB();
      updateLed();
      updateBeep();
      pidGyro(0, 2, 0, 0);
    }
    intermitente('A');
    distAnterior = 800;
  } else if (rojoCerca()) {
    intermitente('D');
    while (abs(getCarAngle()) < 70) {
      updateMPU();
      enviarSPIA();
      enviarSPIB();
      updateLed();
      updateBeep();
      pidGyro(90, 2, 0, 0);
    }
    intermitente('I');
    while (abs(getCarAngle()) > 5 or i2c.TOF[0] > mediaTOFbloque) {
      updateMPU();
      enviarSPIA();
      enviarSPIB();
      updateLed();
      updateBeep();
      pidGyro(0, 2, 0, 0);
    }
    intermitente('A');
    distAnterior = 200;
  }
  else {
    commandB.distBloqueCerca = 70;
    commandB.distBloqueLejos = 120;
    distAnterior = 500;
  }
  while (i2c.TOF[0] < mediaTOF0direccion and i2c.TOF[1] < mediaTOF1direccion) updateRobot();
  beep(100);
  activarHL();
  motorBreak(-15);
  bool sentidoLeido = false;
  long tiempo = millis() + 100;
  bool motorEncendido = false;
  while (!sentidoLeido) {
    updateRobot();
    if (i2c.TOF[1] > mediaTOF1direccion) {
      intermitente('D');
      sentidoRonda = 1;
      sentidoLeido = true;
    }
    else if (i2c.TOF[0] > mediaTOF0direccion) {
      intermitente('I');
      sentidoRonda = -1;
      if (distAnterior == 800) distAnterior = 200;
      else if (distAnterior == 200) distAnterior = 800;
      sentidoLeido = true;
    }
    else if (millis() > tiempo and !motorEncendido) {
      motorStart(5);
      motorEncendido = true;
    }
  }
  motorStartPower(0);
  sectorRonda[1] = leerSector();
  desactivarHL();
  moveDistancia(50, 10, 10);
  while (!commandFinished) updateRobot();
}

byte bloqueCerca(byte sector) {
  if (sector == 1 or sector == 3 or sector == 7 or sector == 8) return 1;
  else if (sector == 2 or sector == 4 or sector == 9 or sector == 10) return 2;
  else return 0;
}

byte mirarUltimoBloque(byte sector) {
  if (sector == 1) return 1;
  else if (sector == 2) return 2;
  else if (sector == 3) return 1;
  else if (sector == 4) return 2;
  else if (sector == 5) return 1;
  else if (sector == 6) return 2;
  else if (sector == 7) return 1;
  else if (sector == 8) return 2;
  else if (sector == 9) return 2;
  else if (sector == 10) return 1;
  else if (sector == 11) return 1;
}

void robotStop() {
  motorStartPower(0);
  intermitente('E');
  luzFreno(true);
  while (1) updateRobot();
}

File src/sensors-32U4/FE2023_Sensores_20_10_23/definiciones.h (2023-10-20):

//This tab contains all variables and defined pins needed in the rest of the program
#define LED 13
// Motor & Encoders
#define ENC_MA 0
#define PWM 11
#define MOTOR_DIR 9
#define MOTOR_DIS 10
#define ENC_MB 1
#define ENC_D 2
#define ENC_I 3
#define PULSOS_ENC 28.00
#define MIN_ACCEL_DISTANCE 800 // Minimum distance to go 0-100 safely
#define MIN_DESACCEL_DISTANCE 5000 // Minimum distance to go 100-0 safely
#define V_MAX_PID 80
#define MIN_V_TO_BREAK 6
volatile long encoderMcontador = 0;
volatile long encoderDcontador = 0;
volatile long encoderIcontador = 0;
volatile long encoderDslave = 0;
volatile long encoderIslave = 0;
const long incrementoMinimoEntrePulsos = 550;
const long incrementoMaximoEntrePulos = 60000;
const float diametroRueda = 29; // Tyre diameter in mm
float error, proporcional, integral, derivativo, errorSuma, giro, errorAnterior;
unsigned long incrementoMotor = micros();
bool motorInvertido = false;
unsigned long microsAnteriorMotor = micros();
int speed = 0;
bool activePID = false;
bool activeRampa = false;
bool activeDistance = false;
bool activeDistAcel = false;
bool breakBitState = false;
bool distanceBitState = false;
bool rampaBitState = false;
bool PIDBitState = false;
bool PWMBitState = false;
long vInicial;
long vFinal;
unsigned long vMaxDist;
bool desacelBreak = false;

//Ultrasonics
#include <NewPing.h>
#define TRIGGER_IZQUIERDO A0 
#define ECHO_IZQUIERDO A1
#define TRIGGER_DERECHO A4
#define ECHO_DERECHO A5
#define TRIGGER_CENTRO A3
#define ECHO_CENTRO A2 
#define SONAR_NUM 3
#define NO_ECHO 255
#define ITERATIONS     5 // Number of iterations.
#define PING_INTERVAL 33 // Milliseconds between sensor pings.
#define MAX_DISTANCE_CENTRO 200 // Maximum distance (in cm) to ping the center US.
#define MAX_DISTANCE 90 // Maximum distance (in cm) to ping the lateral USs.
NewPing sonar[SONAR_NUM] = {   // Sensor object array.
  NewPing(TRIGGER_IZQUIERDO, ECHO_IZQUIERDO, MAX_DISTANCE), // Each sensor's trigger pin, echo pin, and max distance to ping.
  NewPing(TRIGGER_CENTRO, ECHO_CENTRO, MAX_DISTANCE_CENTRO),
  NewPing(TRIGGER_DERECHO, ECHO_DERECHO, MAX_DISTANCE)
};
unsigned long pingTimer[SONAR_NUM]; // Holds the times when the next ping should happen for each sensor.
volatile uint8_t currentSensor = 0;          // Keeps track of which sensor is active.
bool newLecture = false;
volatile uint8_t currentIteration = 0;        // Keeps track of iteration step.
volatile unsigned int timeRAW[SONAR_NUM][ITERATIONS];
bool activeUS[3] = {true, true, true};
unsigned long lastPing = millis();
volatile bool echoCheckFlag = true; 

// SPI
#include <SPI.h>
#define STARTBYTE 251
#define ENDBYTE 252
#define PIN_INTERRUPCION 7
volatile bool haveData = false;
struct datos { // 10 data bytes
  const byte startByte = STARTBYTE;
  byte sr04[3] = {13, 57, 131} ; //Ultrasonics
  unsigned int encoderI = 0; //Encoders
  unsigned int encoderD = 0;
  int velocidad = 0;
  bool lastCommandFlag = 0;
  const byte endByte = ENDBYTE;
};
volatile datos sensor;

struct infoCommands { // 10 data bytes
  const byte startByte = STARTBYTE;
  byte motor; //Motor
  byte motorFlags; //Motor
  byte flags; // Every single bit is used as a different flag in the slave microcontroller
  int distance; // Indicates the distance for the car to move
  int vMaxDistance; // Indicates the max velocity for the car to move a distance
  byte masComandos[3] = {2, 3, 4}; // Extra trash data to complete the number of bytes
  const byte endByte = ENDBYTE;
};
volatile infoCommands command;
volatile byte buff[sizeof(command)];

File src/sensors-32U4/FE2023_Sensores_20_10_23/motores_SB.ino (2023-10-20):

void motorSetup() {
  pinMode(ENC_MA, INPUT_PULLUP);
  pinMode(ENC_MB, INPUT_PULLUP);
  pinMode(ENC_D, INPUT_PULLUP);
  pinMode(ENC_I, INPUT_PULLUP);
  pinMode(PWM, OUTPUT);
  pinMode(MOTOR_DIR, OUTPUT);
  pinMode(MOTOR_DIS, OUTPUT);
  attachInterrupt(digitalPinToInterrupt(ENC_MA), encoderM, RISING);
  attachInterrupt(digitalPinToInterrupt(ENC_D), encoderD, RISING);
  attachInterrupt(digitalPinToInterrupt(ENC_I), encoderI, RISING);
}

void encoderM() {
  if (!digitalRead(MOTOR_DIR)) encoderMcontador++;
  else encoderMcontador--;
  incrementoMotor = micros() - microsAnteriorMotor;
  microsAnteriorMotor = micros();
}

void encoderD() {
  encoderDcontador++;
  encoderDslave++;
}

void encoderI() {
  encoderIcontador++;
  encoderIslave++;
}

long motorGetCount(String motor) {                //Returns the pulses done by the tyre
  if (motor == "D")return encoderDcontador;
  else if (motor == "I")return encoderIcontador;
  else if (motor == "M")return encoderMcontador;
}

long motorGetSlaveCount(String motor) {                //Returns the pulses done by the tyre
  if (motor == "D")return encoderDslave;
  else if (motor == "I")return encoderIslave;
}

void motorResetCount(String motor) {            //Restarts the encoder counter
  for (int i = 0; i < motor.length(); i++) {
    if (motor.charAt(i) == 'D') encoderDcontador = 0;
    else if (motor.charAt(i) == 'I') encoderIcontador = 0;
    else if (motor.charAt(i) == 'M') encoderMcontador = 0;
  }
}

void motorResetSlaveCount(String motor) {            //Restarts the encoder counter
  for (int i = 0; i < motor.length(); i++) {
    if (motor.charAt(i) == 'D') encoderDslave = 0;
    else if (motor.charAt(i) == 'I') encoderIslave = 0;
  }
}

long motorGetSlaveDistance(String motor) {                //Returns the distance in mm done by the tyre
  if (motor == "D")return ((encoderDslave / PULSOS_ENC) * PI * diametroRueda);
  else if (motor == "I")return ((encoderIslave / PULSOS_ENC) * PI * diametroRueda);
}

unsigned int motorGetDistancia(String motor) {            //Returns the distance in mm done by the tyre
  if (motor == "D")return ((encoderDcontador / PULSOS_ENC) * PI * diametroRueda);
  else if (motor == "I")return ((encoderIcontador / PULSOS_ENC) * PI * diametroRueda);
}

void updateMotor() {
  long diferenciaMicros = micros() - microsAnteriorMotor;
  if (diferenciaMicros > incrementoMaximoEntrePulos) {
    incrementoMotor = 100000; // Con este valor la velocidad se hace 0
  }
}

void motorStartPower(int vel) {
  vel = constrain(vel, -100, 100);
  int velPwm = map (abs(vel), 0, 100, 0, 255);
  if (vel < 0) digitalWrite(MOTOR_DIR, 1);
  else if (vel > 0)digitalWrite(MOTOR_DIR, 0);
  analogWrite (PWM, velPwm);
}

int motorGetSpeed() {  // Returns the real velocity -100 - 100
  int vel = 0;
  if (incrementoMotor > 10000) vel = (incrementoMinimoEntrePulsos * 100) / incrementoMotor;
  else vel = (10000 / (incrementoMotor - 550) + 6);
  vel = constrain(vel, -100, 100);
  if (digitalRead(MOTOR_DIR)) vel = vel * (-1);
  return vel;
}

void motorStart(int velocidad) { // PID control for a certain velocity
  if (velocidad == 0) {
    motorStartPower(0);
    return;
  }
  float kp = 3, ki = 0.01, kd = 3;
  velocidad = constrain(velocidad, -100, 100);
  updateMotor();
  error = motorGetSpeed() - velocidad;
  proporcional = error * kp;
  errorSuma = errorSuma + error;
  if (errorAnterior * error < 0) errorSuma = 0;
  integral = errorSuma * ki;
  derivativo = (error - errorAnterior) * kd;
  errorAnterior = error;
  giro = proporcional + integral + derivativo;
  if (velocidad > 0) {
    motorStartPower(constrain(velocidad - (int)giro, 0, 100));
  }
  else if (velocidad < 0) {
    motorStartPower(constrain(velocidad - (int)giro, -100, 0));
  }
}

void motorStart(int velocidad, bool freno) {
  if (velocidad == 0) {
    motorStartPower(0);
    return;
  }
  float kp = 3, ki = 0.01, kd = 3; // definir de forma local
  velocidad = constrain(velocidad, -100, 100);
  updateMotor();
  error = motorGetSpeed() - velocidad;
  proporcional = error * kp;
  errorSuma = errorSuma + error;
  if (errorAnterior * error < 0) errorSuma = 0;
  integral = errorSuma * ki;
  derivativo = (error - errorAnterior) * kd;
  errorAnterior = error;
  giro = proporcional + integral + derivativo;
  if (velocidad > 0) {
    if (freno) motorStartPower(constrain(velocidad - (int)giro, -20, 100));
    else motorStartPower(constrain(velocidad - (int)giro, 0, 100));
  }
  else if (velocidad < 0) {
    if (freno) motorStartPower(constrain(velocidad - (int)giro, -100, 20));
    else motorStartPower(constrain(velocidad - (int)giro, -100, 0));
  }
}

void motorStart(int velocidad, bool freno, float kp, float ki, float kd) {
  if (velocidad == 0) {
    motorStartPower(0);
    return;
  }
  velocidad = constrain(velocidad, -100, 100);
  updateMotor();
  error = motorGetSpeed() - velocidad;
  proporcional = error * kp;
  errorSuma = errorSuma + error;
  if (errorAnterior * error < 0) errorSuma = 0;
  integral = errorSuma * ki;
  derivativo = (error - errorAnterior) * kd;
  errorAnterior = error;
  giro = proporcional + integral + derivativo;
  if (velocidad > 0) {
    if (freno) motorStartPower(constrain(velocidad - (int)giro, -20, 100));
    else motorStartPower(constrain(velocidad - (int)giro, 0, 100));
  }
  else if (velocidad < 0) {
    if (freno) motorStartPower(constrain(velocidad - (int)giro, -100, 20));
    else motorStartPower(constrain(velocidad - (int)giro, -100, 0));
  }
}

bool acelExpo(int velInicial, int velFinal) {          // Makes an acceleration and returns 1 when finished
  velInicial = constrain(velInicial, 2, 100);
  velFinal = constrain(velFinal, 0, 100);
  const float distInicial = (velInicial * MIN_ACCEL_DISTANCE) / 100;
  float velocidad = ((distInicial + motorGetSlaveDistance("D")) / MIN_ACCEL_DISTANCE) * 100;
  if (velocidad <= velFinal) {
    if (velocidad >= V_MAX_PID) motorStartPower(velocidad);
    else motorStart(velocidad);
    return 0;
  }
  else return 1;
}

bool desacelExpo(int velInicial, int velFinal) { // Makes a decceleration and returns 1 when finished
  velInicial = constrain(velInicial, 0, 100);
  velFinal = constrain(velFinal, 0, 100);
  if (velFinal == 0) {
    desacelBreak = true;
    velFinal = MIN_V_TO_BREAK;
  }
  const float distInicial = ((100 - velInicial) / 100.00) * MIN_DESACCEL_DISTANCE;
  float velocidad = (((motorGetSlaveDistance("D") + distInicial) / MIN_DESACCEL_DISTANCE) * (-100)) + 100;
  if (velocidad >= velFinal) {
    if (velocidad > V_MAX_PID) motorStartPower(velocidad);
    else motorStart(velocidad);
    return 0;
  }
  else {
    if (desacelBreak) motorStartPower(0);
    desacelBreak = false;
    return 1;
  }
}

void motorBreak() {
  digitalWrite(MOTOR_DIR, !digitalRead(MOTOR_DIR));
  analogWrite (PWM, 0);
  activeDistance = false;
  activeRampa = false;
  activePID = false;
}
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

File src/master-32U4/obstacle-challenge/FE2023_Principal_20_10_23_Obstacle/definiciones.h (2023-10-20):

#define BTN 6
#define BUZZ 5
#define DIR A5
#define LED 13
#include <Servo.h>
#define OFFSET_SERVO -6
float error, proporcional, integral, derivativo, errorSuma, giro, errorAnterior;
long beepTime = 0;
bool beepDone = false;
int distAnterior = 0;
#define mediaTOFbloque 600
#define mediaTOFpared 1200
#define mediaTOF0direccion 1300
#define mediaTOF1direccion 1500
const int offsetUS = 120;
byte sectorRonda[4] = {0, 0, 0, 0};
int sentidoRonda = 0;
byte vuelta = 0;
int vMaxSector = 10;
int vMinSector = 10;
#define TIEMPO_BLOQUE 500
int dirAnteriorCurva = 0;

//SPI
#include <SPI.h>
#define SSA A4
#define SSB A3
#define STARTBYTE 251 // Only as a start flag
#define ENDBYTE 252 // // Only as an end flag
long SPIA_Interval = 5; // Delay in milliseconds
long lastTimeSPIA = millis();
long SPIB_Interval = 5; // Delay in milliseconds
long lastTimeSPIB = millis();

//MPU6050
#include <MPU6050_light.h>
#include "Wire.h"
float ypr[3];           // [yaw, pitch, roll]   yaw/pitch/roll container and gravity vector.
float offsetMPU = 0.0;

// MOTORS
unsigned int offsetD = 0;
unsigned int offsetI = 0;
///////////////////////////SENSORS SLAVE STRUCTURE////////////////
struct datosA { // 10 data bytes (start and end bytes are not counted as data bytes)
  const byte startByte = STARTBYTE;
  byte sr04[3];
  unsigned int encoderI;
  unsigned int encoderD;
  int velocidad;
  bool lastCommandFlag = 0;
  const byte endByte = ENDBYTE;
};
datosA sensor;

bool lastCommandAState = 0;
bool commandFinished = false;
byte buffA[sizeof(sensor)];

struct infoCommandsA { // 10 data bytes
  const byte startByte = STARTBYTE;
  byte motor; //Motor
  byte motorFlags; //Motor
  byte flags = 0; // Every single bit is used as a different flag in the slave microcontroller
  int distance; // Indicates the distance for the car to move
  int vMaxDistance; // Indicates the max velocity for the car to move a distance
  byte masComandos[3] = {2, 3, 4}; // Extra commands to fill the rest of the data bytes
  const byte endByte = ENDBYTE;
};
infoCommandsA commandA;

///////////////////////////I2C SLAVE STRUCTURE////////////////
struct datosB { // 9 data bytes
  const byte startByte = STARTBYTE;
  byte sector;
  unsigned int TOF[2];
  int quitar;
  byte bloqueCerca;
  byte lastCommandFlag;
  const byte endByte = ENDBYTE;
};
datosB i2c;

bool lastCommandBState = 0;
bool servoFinished = false;
byte buffB[sizeof(i2c)] = {0};

struct infoCommandsB { // 9 data bytes
  const byte startByte = STARTBYTE;
  bool activeCam = 1;
  byte angServo = 90;
  byte leds = 0;
  byte filtroCam = 0;
  byte distBloqueCerca = 95;
  byte distBloqueLejos = 145;
  byte masComandos[3] = {24, 7, 0};
  const byte endByte = ENDBYTE;
};
infoCommandsB commandB;

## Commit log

2021-10-09 Ultrasonic 3D models
2021-10-09 Encoder 3D models
    [Encoder cage.stl, Encoder gear.stl, Encoder top.stl]
2021-10-09 Create Poner esquematico y stl
2023-10-20 Delete src/I2C-32U4/FE2023_SensoresI2C_16_09_23 directory
    Update program
